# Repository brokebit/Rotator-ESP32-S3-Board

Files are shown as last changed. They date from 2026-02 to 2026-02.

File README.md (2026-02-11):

# Rotator-ESP32-S3-Board

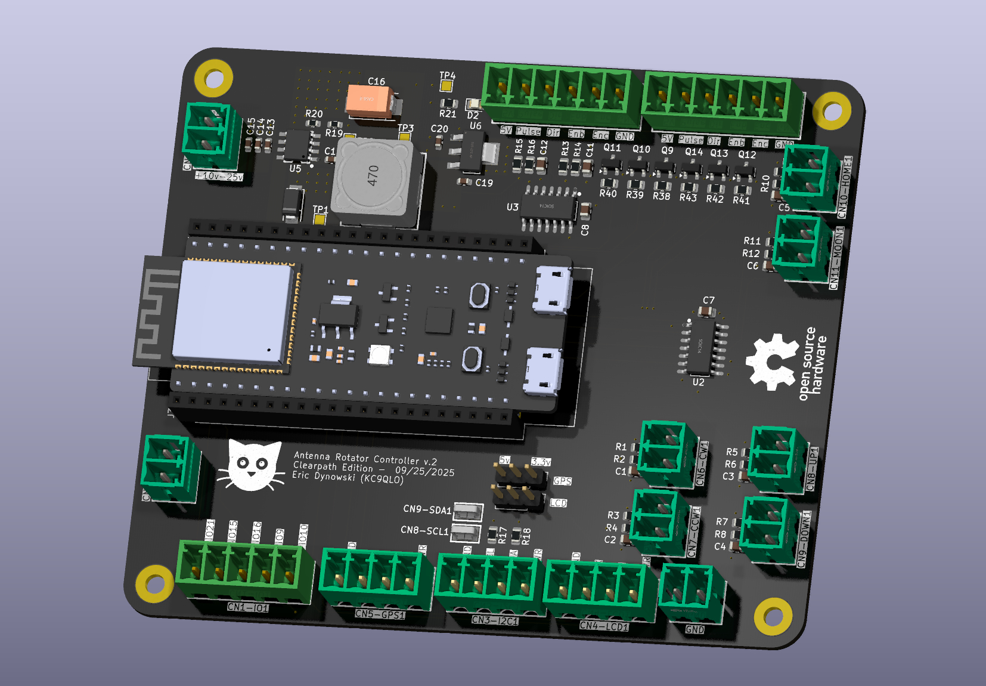
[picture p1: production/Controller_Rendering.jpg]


# Features / Design Info
- One of the ESP32 serial ports exposes a GS-232 interface for motor control commands for connecting to a PC interfacing with rotctld from the Hamlib suite
- GPS Time Sync using NEMA GPS Module over RS232
- Serial interface for Nextion Display
- Designed for Clearpath servo motors from https://teknic.com/
- Interface for 6 Hardware Debounced buttons for manual direction control, homing and moon tracking 
- Uses pulse encoder data from the Clearpath motors for position feedback
- Power input is +10v - +25v DC
- Motors are powered by seperate power source 
- Voltage select headers to select either 3.3v or 5v logic for RS232 interfaces (GPS, LCD)
- 6 Layer Board

# Build Pics
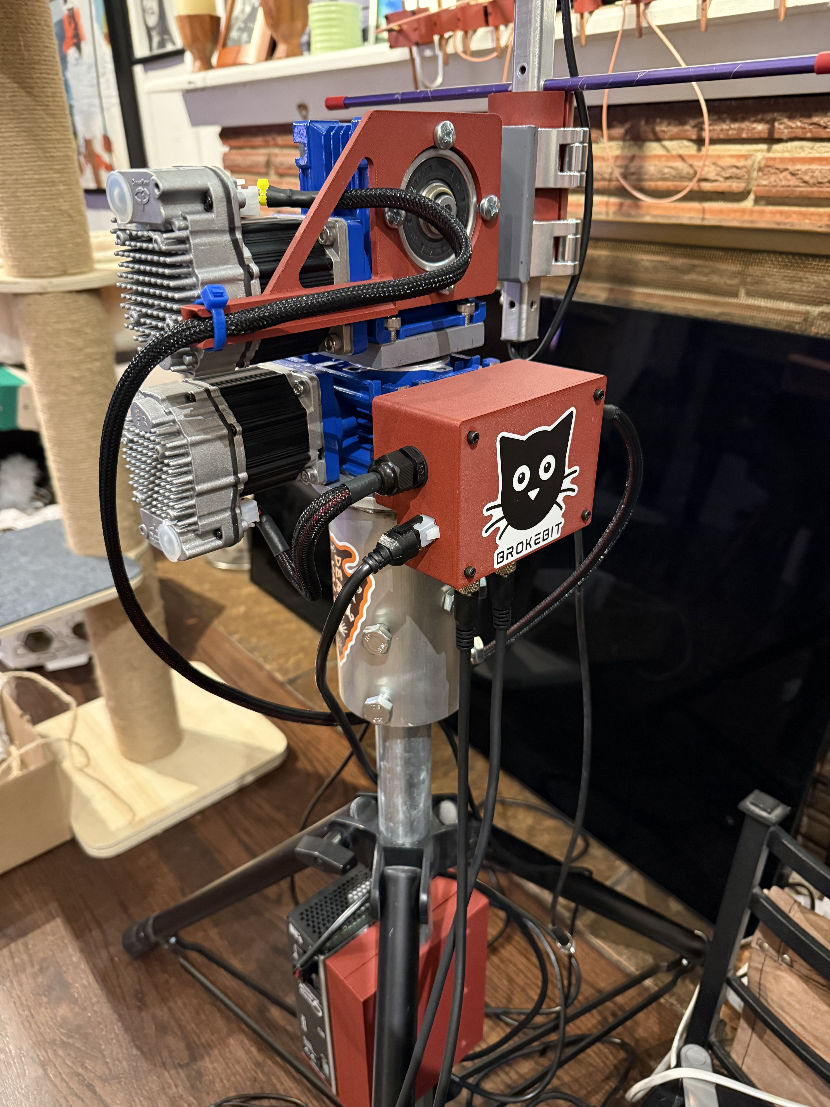
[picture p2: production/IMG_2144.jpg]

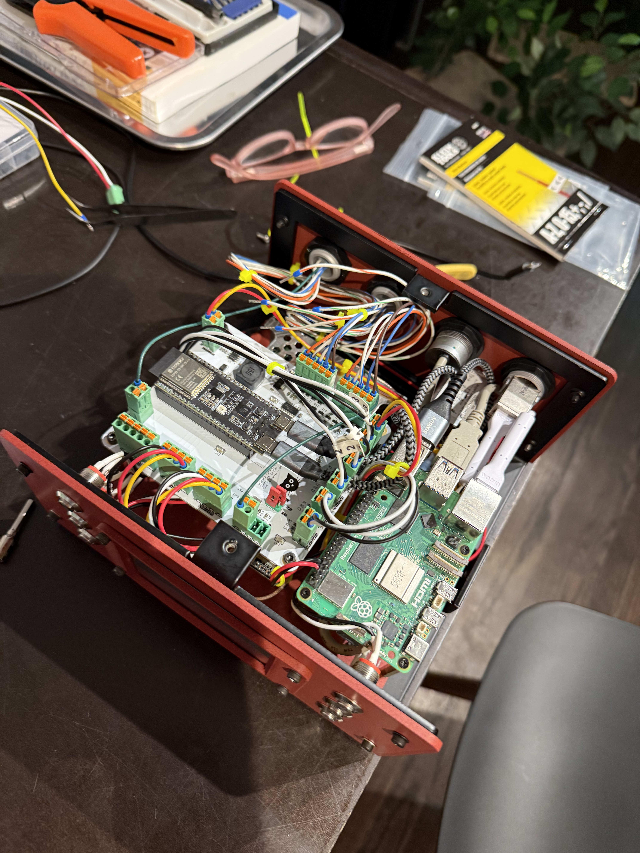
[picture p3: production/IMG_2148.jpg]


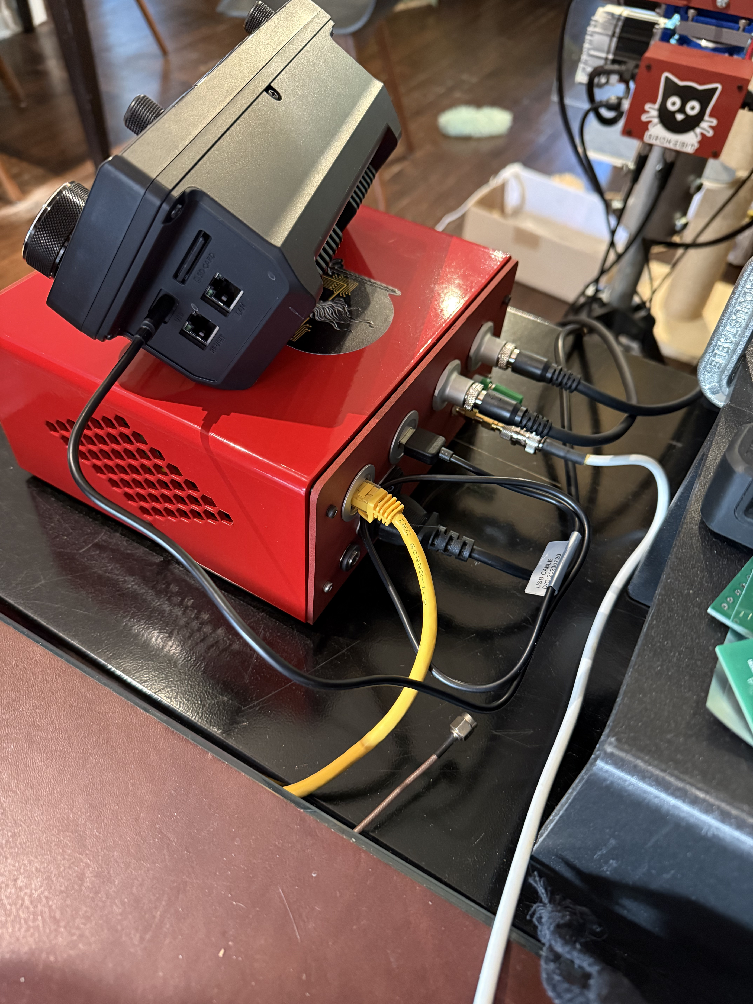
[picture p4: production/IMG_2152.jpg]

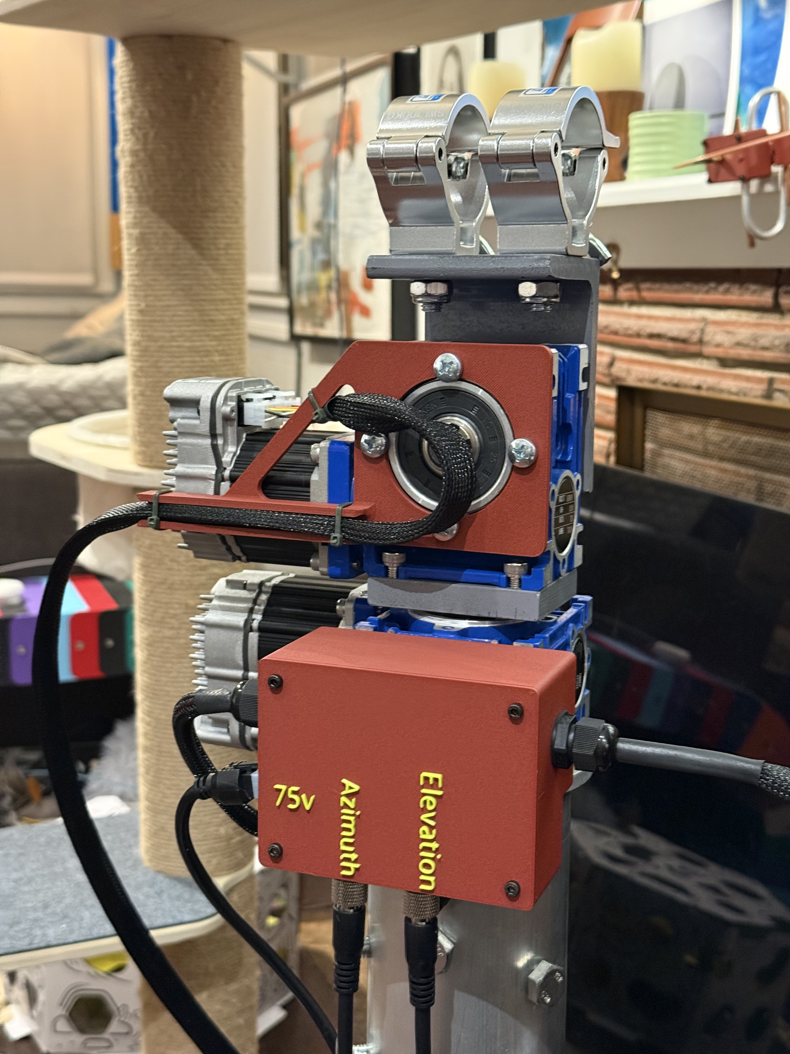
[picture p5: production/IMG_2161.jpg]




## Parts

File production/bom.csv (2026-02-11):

Designator | Footprint | Quantity | Value | LCSC Part #
C1, C11, C12, C2, C3, C4, C5, C6, C7, C8 | 0805 | 10 | .1uf
C13, C14, C15, C19, C20 | 0603 | 5 | 10uf
C16 | CAP-SMD_L7.3-W4.3-R-RD | 1 | 330uF | C79112
C17 | 0603 | 1 | 10nf
CN1-IO1 | CONN-TH_WJ15EDGVC-3.81-5P | 1 | WJ15EDGVC-3.81-5P | C8391
CN10-HOME1, CN11-MOON1, CN12-RST1, CN13-PWR2, CN5, CN6-CW1, CN7-CCW1, CN8-UP1, CN9-DOWN1 | CONN-TH_2P-P3.81_KF2EDGV-3.81-2P | 9 | KF2EDGV-3.81-2P | C441332
CN3-I2C1, CN4-LCD1, CN5-GPS1 | CONN-TH_4P-P3.81_WJ2EDGVC-3.81-4P | 3 | WJ15EDGVC-3.81-4P | C8410
CN8-SCL1, CN9-SDA1 | TESTPOINT-SMD_L3.8-W2.0_RH-5019 | 2 | RH-5019 | C5199800
D1 | SMA_L4.3-W2.6-LS5.1-RD | 1 | B340A | C64982
D2 | 0805 | 1 | LED | C84260
J1 | PinHeader_1x03_P2.54mm_Vertical | 1 | LCD_PWR_SELECT
J2 | PinHeader_1x03_P2.54mm_Vertical | 1 | GPS_PWR_SELECT
J3, J4 | PinSocket_1x22_P2.54mm_Vertical | 2 | Conn_01x22_Socket
L1 | IND-SMD_L12.5-W12.5_RLF12545T | 1 | 15uH | C40000
P1, P2 | CONN-TH_6P_WJ15EDGVC-3.81-6P | 2 | WJ15EDGVC-6P | C8415
Q10, Q11, Q12, Q13, Q14, Q9 | SOT-23 | 6 | MMBT3904
R1, R10, R11, R12, R13, R14, R15, R16, R17, R18, R2, R3, R4, R5, R6, R7, R8, R9 | 0805 | 18 | 10k
R19 | 0603 | 1 | 10k
R20 | 0603 | 1 | 3.24k
R21 | 0805 | 1 | 40 | C2930194
R38, R39, R40, R41, R42, R43 | 0805 | 6 | 4.7k
TP1, TP2, TP3, TP4 | TestPoint_Pad_1.5x1.5mm | 4 | TestPoint
U1 | ESP32-S3-DevKitC | 1 | ESP32-S3-DevKitC
U2, U3 | SOIC-14_L8.7-W3.9-P1.27-LS6.0-BL | 2 | 74HC14D,653 | C5605
U5 | ESOP-8_L4.9-W3.9-P1.27-LS6.0-TL-EP | 1 | TPS5430DDAR | C9864
U6 | SOT-223-4_L6.5-W3.5-P2.30-LS7.0-BR | 1 | AMS1117-3.3_C347222 | C347222

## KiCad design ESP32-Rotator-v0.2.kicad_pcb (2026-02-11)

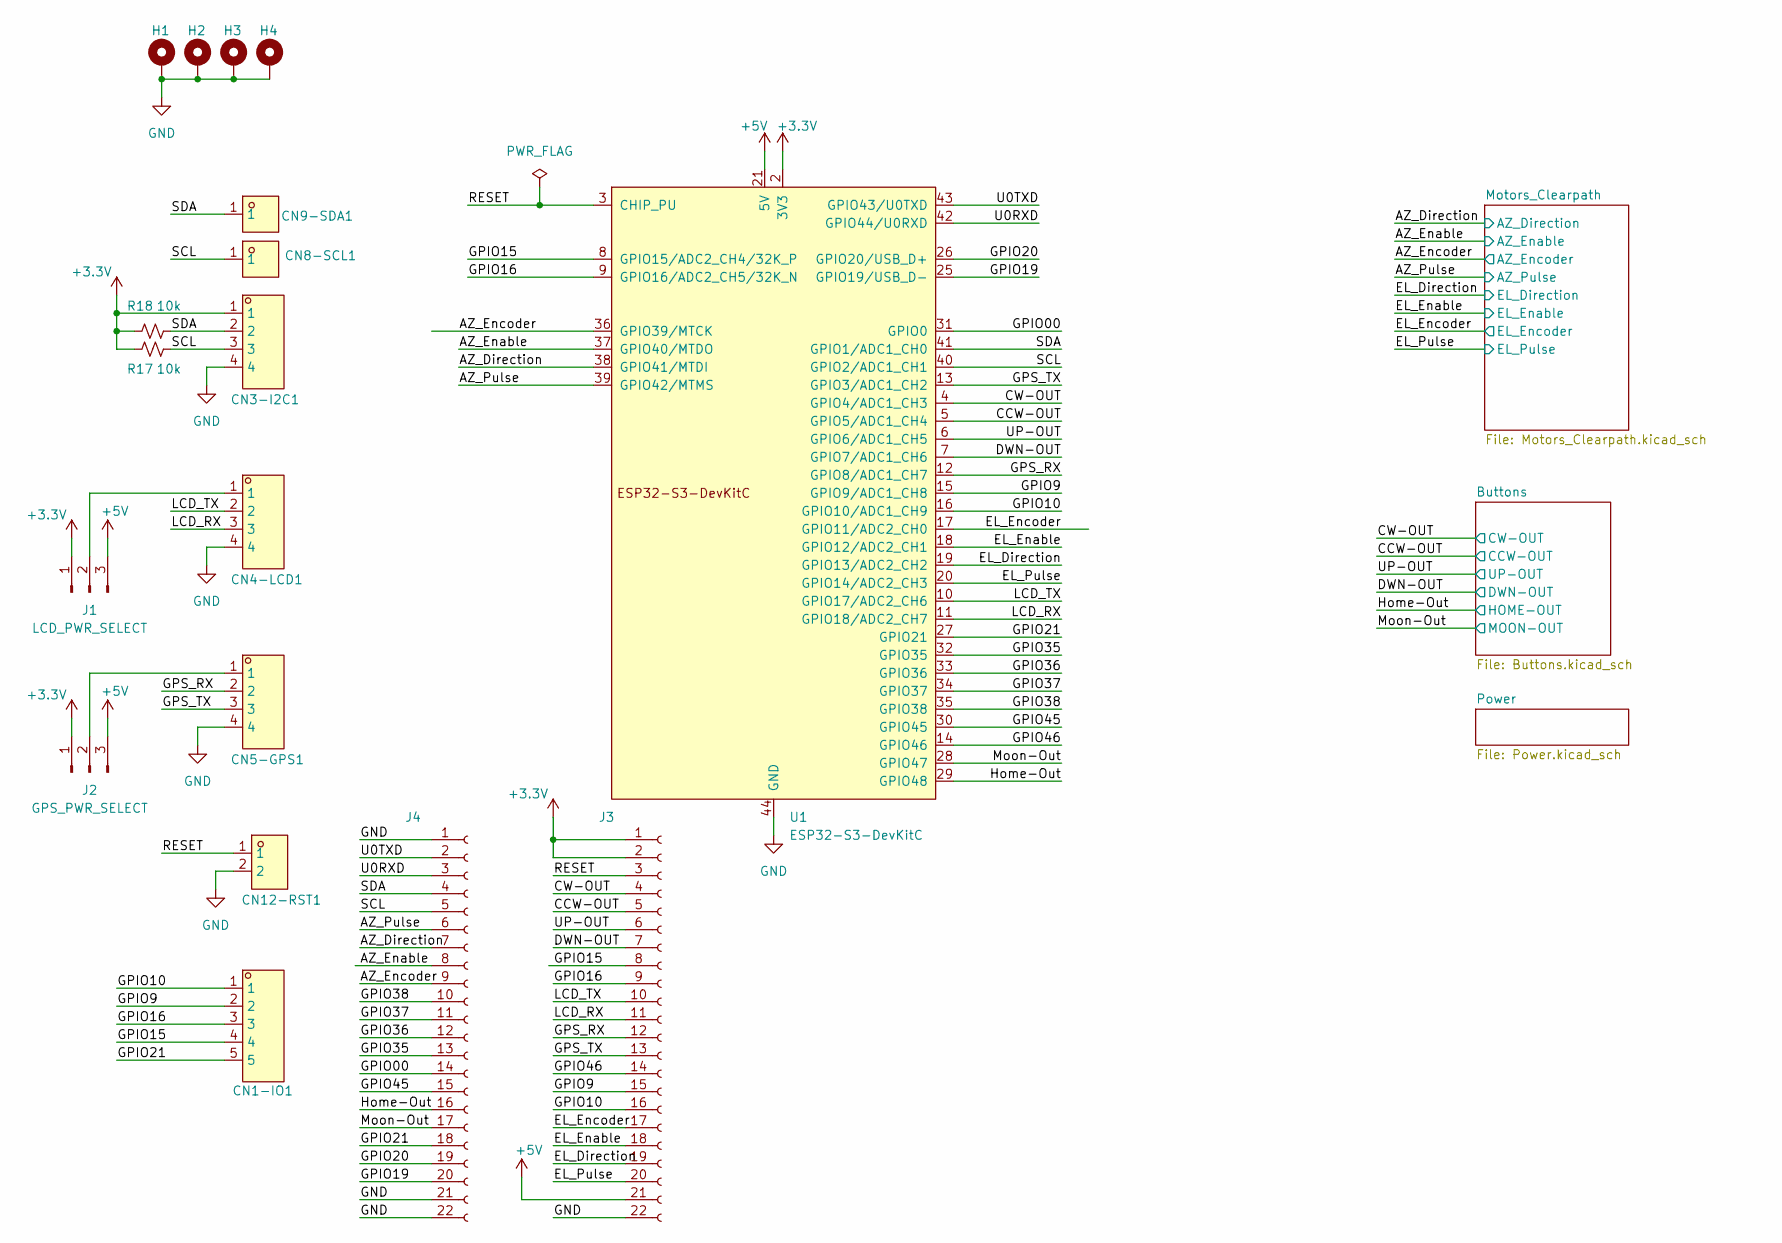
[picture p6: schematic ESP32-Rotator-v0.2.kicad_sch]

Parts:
CN1-IO1: WJ15EDGVC-3.81-5P; CONN-TH_WJ15EDGVC-3.81-5P; LCSC Part C8391
CN3-I2C1, CN4-LCD1, CN5-GPS1: WJ15EDGVC-3.81-4P; CONN-TH_4P-P3.81_WJ2EDGVC-3.81-4P; LCSC Part C8410
CN8-SCL1, CN9-SDA1: RH-5019; TESTPOINT-SMD_L3.8-W2.0_RH-5019; LCSC Part C5199800
CN12-RST1: KF2EDGV-3.81-2P; CONN-TH_2P-P3.81_KF2EDGV-3.81-2P; LCSC Part C441332
H1, H2, H3, H4: MountingHole_Pad; MountingHole_3.2mm_M3_Pad
J1: LCD_PWR_SELECT; PinHeader_1x03_P2.54mm_Vertical
J2: GPS_PWR_SELECT; PinHeader_1x03_P2.54mm_Vertical
J3, J4: Conn_01x22_Socket; PinSocket_1x22_P2.54mm_Vertical
R17, R18: 10k; R_0805_2012Metric
U1: ESP32-S3-DevKitC

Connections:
+3.3V: CN3-I2C1.1, J1.1, J2.1, J3.1, J3.2, R17.1, R18.1, U1.1 (3V3), U1.2 (3V3); also elsewhere on the board
+5V: J1.3, J2.3, J3.21, U1.21 (5V); also elsewhere on the board
/AZ_Direction: J4.7, U1.38 (GPIO41/MTDI); also elsewhere on the board
/AZ_Enable: J4.8, U1.37 (GPIO40/MTDO); also elsewhere on the board
/AZ_Encoder: J4.9, U1.36 (GPIO39/MTCK); also elsewhere on the board
/AZ_Pulse: J4.6, U1.39 (GPIO42/MTMS); also elsewhere on the board
/CCW-OUT: J3.5, U1.5 (GPIO5/ADC1_CH4); also elsewhere on the board
/CW-OUT: J3.4, U1.4 (GPIO4/ADC1_CH3); also elsewhere on the board
/DWN-OUT: J3.7, U1.7 (GPIO7/ADC1_CH6); also elsewhere on the board
/EL_Direction: J3.19, U1.19 (GPIO13/ADC2_CH2); also elsewhere on the board
/EL_Enable: J3.18, U1.18 (GPIO12/ADC2_CH1); also elsewhere on the board
/EL_Encoder: J3.17, U1.17 (GPIO11/ADC2_CH0); also elsewhere on the board
/EL_Pulse: J3.20, U1.20 (GPIO14/ADC2_CH3); also elsewhere on the board
/GPIO00: J4.14, U1.31 (GPIO0)
/GPIO9: CN1-IO1.2, J3.15, U1.15 (GPIO9/ADC1_CH8)
/GPIO10: CN1-IO1.1, J3.16, U1.16 (GPIO10/ADC1_CH9)
/GPIO15: CN1-IO1.4, J3.8, U1.8 (GPIO15/ADC2_CH4/32K_P)
/GPIO16: CN1-IO1.3, J3.9, U1.9 (GPIO16/ADC2_CH5/32K_N)
/GPIO19: J4.20, U1.25 (GPIO19/USB_D-)
/GPIO20: J4.19, U1.26 (GPIO20/USB_D+)
/GPIO21: CN1-IO1.5, J4.18, U1.27 (GPIO21)
/GPIO35: J4.13, U1.32 (GPIO35)
/GPIO36: J4.12, U1.33 (GPIO36)
/GPIO37: J4.11, U1.34 (GPIO37)
/GPIO38: J4.10, U1.35 (GPIO38)
/GPIO45: J4.15, U1.30 (GPIO45)
/GPIO46: J3.14, U1.14 (GPIO46)
/GPS_RX: CN5-GPS1.2, J3.12, U1.12 (GPIO8/ADC1_CH7)
/GPS_TX: CN5-GPS1.3, J3.13, U1.13 (GPIO3/ADC1_CH2)
/Home-Out: J4.16, U1.29 (GPIO48); also elsewhere on the board
/LCD_RX: CN4-LCD1.3, J3.11, U1.11 (GPIO18/ADC2_CH7)
/LCD_TX: CN4-LCD1.2, J3.10, U1.10 (GPIO17/ADC2_CH6)
/Moon-Out: J4.17, U1.28 (GPIO47); also elsewhere on the board
/RESET: CN12-RST1.1, J3.3, U1.3 (CHIP_PU)
/SCL: CN3-I2C1.3, CN8-SCL1.1, J4.5, R17.2, U1.40 (GPIO2/ADC1_CH1)
/SDA: CN3-I2C1.2, CN9-SDA1.1, J4.4, R18.2, U1.41 (GPIO1/ADC1_CH0)
/U0RXD: J4.3, U1.42 (GPIO44/U0RXD)
/U0TXD: J4.2, U1.43 (GPIO43/U0TXD)
/UP-OUT: J3.6, U1.6 (GPIO6/ADC1_CH5); also elsewhere on the board
GND: CN3-I2C1.4, CN4-LCD1.4, CN5-GPS1.4, CN12-RST1.2, H1.1, H2.1, H3.1, H4.1, J3.22, J4.1, J4.21, J4.22, U1.22 (GND), U1.23 (GND), U1.24 (GND), U1.44 (GND); also elsewhere on the board
unnamed: CN4-LCD1.1, J1.2
unnamed: CN5-GPS1.1, J2.2

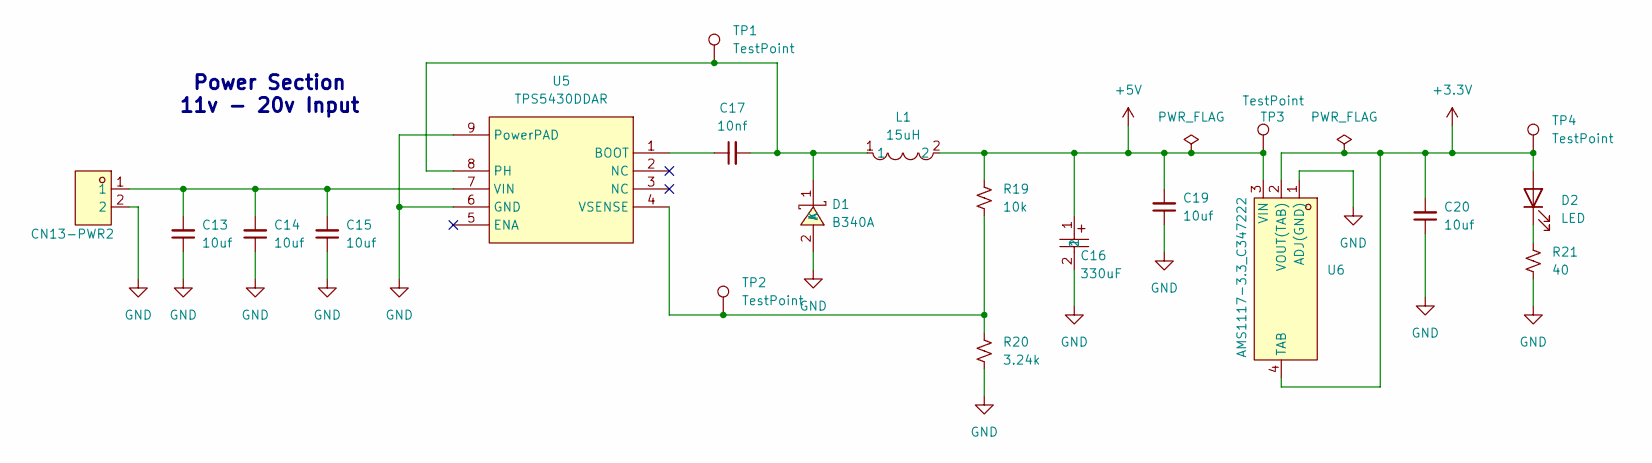
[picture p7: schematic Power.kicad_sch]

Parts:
C13, C14, C15, C19, C20: 10uf; C_0603_1608Metric
C16: 330uF; CAP-SMD_L7.3-W4.3-R-RD; LCSC Part C79112
C17: 10nf; C_0603_1608Metric
CN13-PWR2: KF2EDGV-3.81-2P; CONN-TH_2P-P3.81_KF2EDGV-3.81-2P; LCSC Part C441332
D1: B340A; SMA_L4.3-W2.6-LS5.1-RD; LCSC Part C64982
D2: LED; LED_0805_2012Metric; LCSC Part C84260
L1: 15uH; IND-SMD_L12.5-W12.5_RLF12545T; LCSC Part C40000
R19: 10k; R_0603_1608Metric
R20: 3.24k; R_0603_1608Metric
R21: 40; R_0805_2012Metric; LCSC Part C2930194
TP1, TP2, TP3, TP4: TestPoint; TestPoint_Pad_1.5x1.5mm
U5: TPS5430DDAR; ESOP-8_L4.9-W3.9-P1.27-LS6.0-TL-EP; LCSC Part C9864
U6: AMS1117-3.3_C347222; SOT-223-4_L6.5-W3.5-P2.30-LS7.0-BR; LCSC Part C347222

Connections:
+3.3V: C20.2, D2.2 (A), TP4.1, U6.2 (VOUT(TAB)), U6.4 (TAB); also elsewhere on the board
+5V: C16.1, C19.2, L1.2, R19.1, TP3.1, U6.3 (VIN); also elsewhere on the board
GND: C13.1, C14.1, C15.1, C16.2, C19.1, C20.1, CN13-PWR2.2, D1.2 (A), R20.2, R21.2, U5.6 (GND), U5.9 (PowerPAD), U6.1 (ADJ(GND)); also elsewhere on the board
unnamed: C17.2, D1.1 (K), L1.1, TP1.1, U5.8 (PH)
unnamed: D2.1 (K), R21.1
unnamed: C17.1, U5.1 (BOOT)
unnamed: C13.2, C14.2, C15.2, CN13-PWR2.1, U5.7 (VIN)
unnamed: R19.2, R20.1, TP2.1, U5.4 (VSENSE)

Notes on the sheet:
Power Section 11v - 20v Input

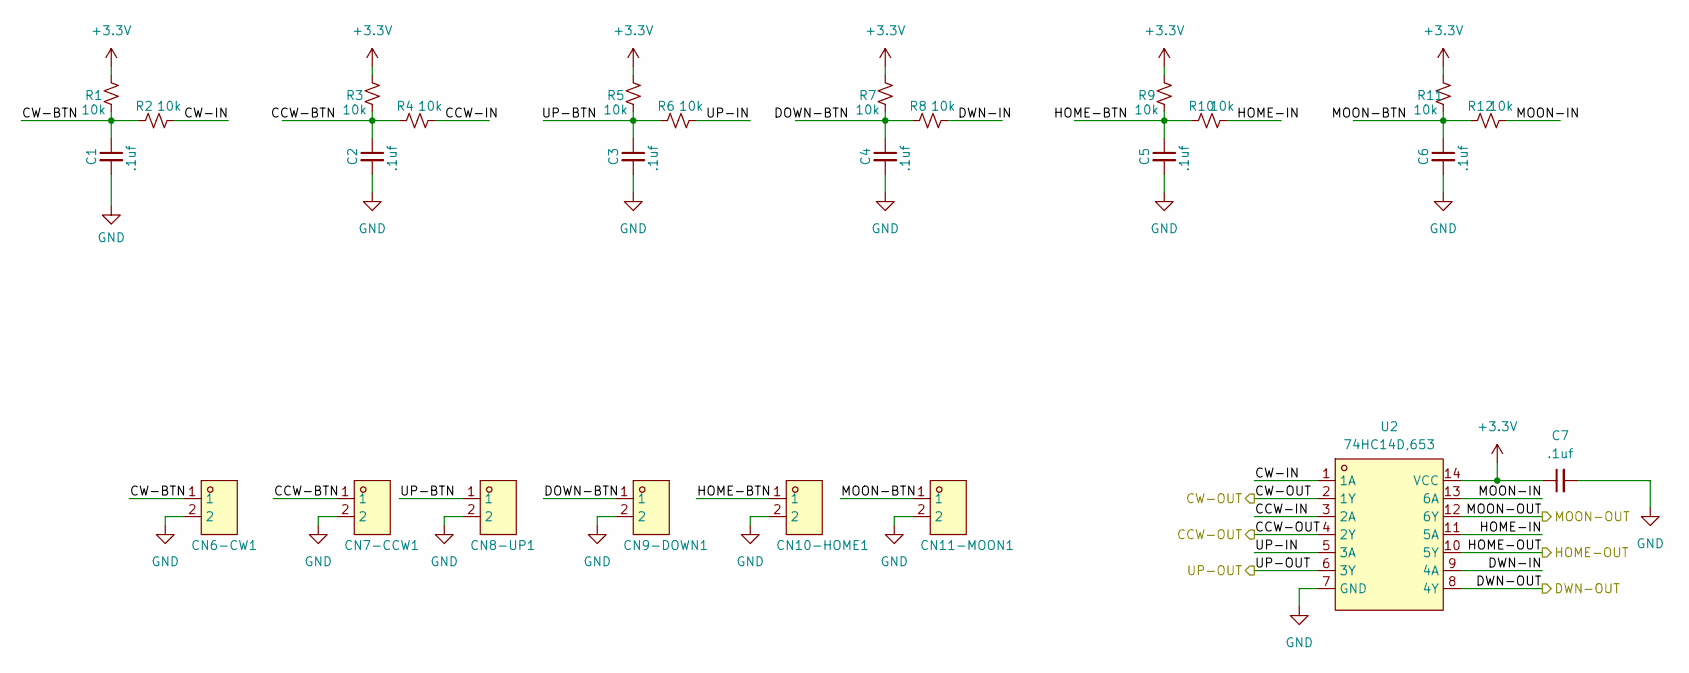
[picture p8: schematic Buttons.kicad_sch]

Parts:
C1, C2, C3, C4, C5, C6, C7: .1uf; C_0805_2012Metric
CN6-CW1, CN7-CCW1, CN8-UP1, CN9-DOWN1, CN10-HOME1, CN11-MOON1: KF2EDGV-3.81-2P; CONN-TH_2P-P3.81_KF2EDGV-3.81-2P; LCSC Part C441332
R1, R2, R3, R4, R5, R6, R7, R8, R9, R10, R11, R12: 10k; R_0805_2012Metric
U2: 74HC14D,653; SOIC-14_L8.7-W3.9-P1.27-LS6.0-BL; LCSC Part C5605

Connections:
+3.3V: C7.1, R1.1, R3.1, R5.1, R7.1, R9.1, R11.1, U2.14 (VCC); also elsewhere on the board
/Buttons/CCW-BTN: C2.1, CN7-CCW1.1, R3.2, R4.2
/Buttons/CCW-IN: R4.1, U2.3 (2A)
/Buttons/CW-BTN: C1.1, CN6-CW1.1, R1.2, R2.2
/Buttons/CW-IN: R2.1, U2.1 (1A)
/Buttons/DOWN-BTN: C4.1, CN9-DOWN1.1, R7.2, R8.2
/Buttons/DWN-IN: R8.1, U2.9 (4A)
/Buttons/HOME-BTN: C5.1, CN10-HOME1.1, R9.2, R10.2
/Buttons/HOME-IN: R10.1, U2.11 (5A)
/Buttons/MOON-BTN: C6.1, CN11-MOON1.1, R11.2, R12.2
/Buttons/MOON-IN: R12.1, U2.13 (6A)
/Buttons/UP-BTN: C3.1, CN8-UP1.1, R5.2, R6.2
/Buttons/UP-IN: R6.1, U2.5 (3A)
/CCW-OUT: U2.4 (2Y); also elsewhere on the board
/CW-OUT: U2.2 (1Y); also elsewhere on the board
/DWN-OUT: U2.8 (4Y); also elsewhere on the board
/Home-Out: U2.10 (5Y); also elsewhere on the board
/Moon-Out: U2.12 (6Y); also elsewhere on the board
/UP-OUT: U2.6 (3Y); also elsewhere on the board
GND: C1.2, C2.2, C3.2, C4.2, C5.2, C6.2, C7.2, CN6-CW1.2, CN7-CCW1.2, CN8-UP1.2, CN9-DOWN1.2, CN10-HOME1.2, CN11-MOON1.2, U2.7 (GND); also elsewhere on the board

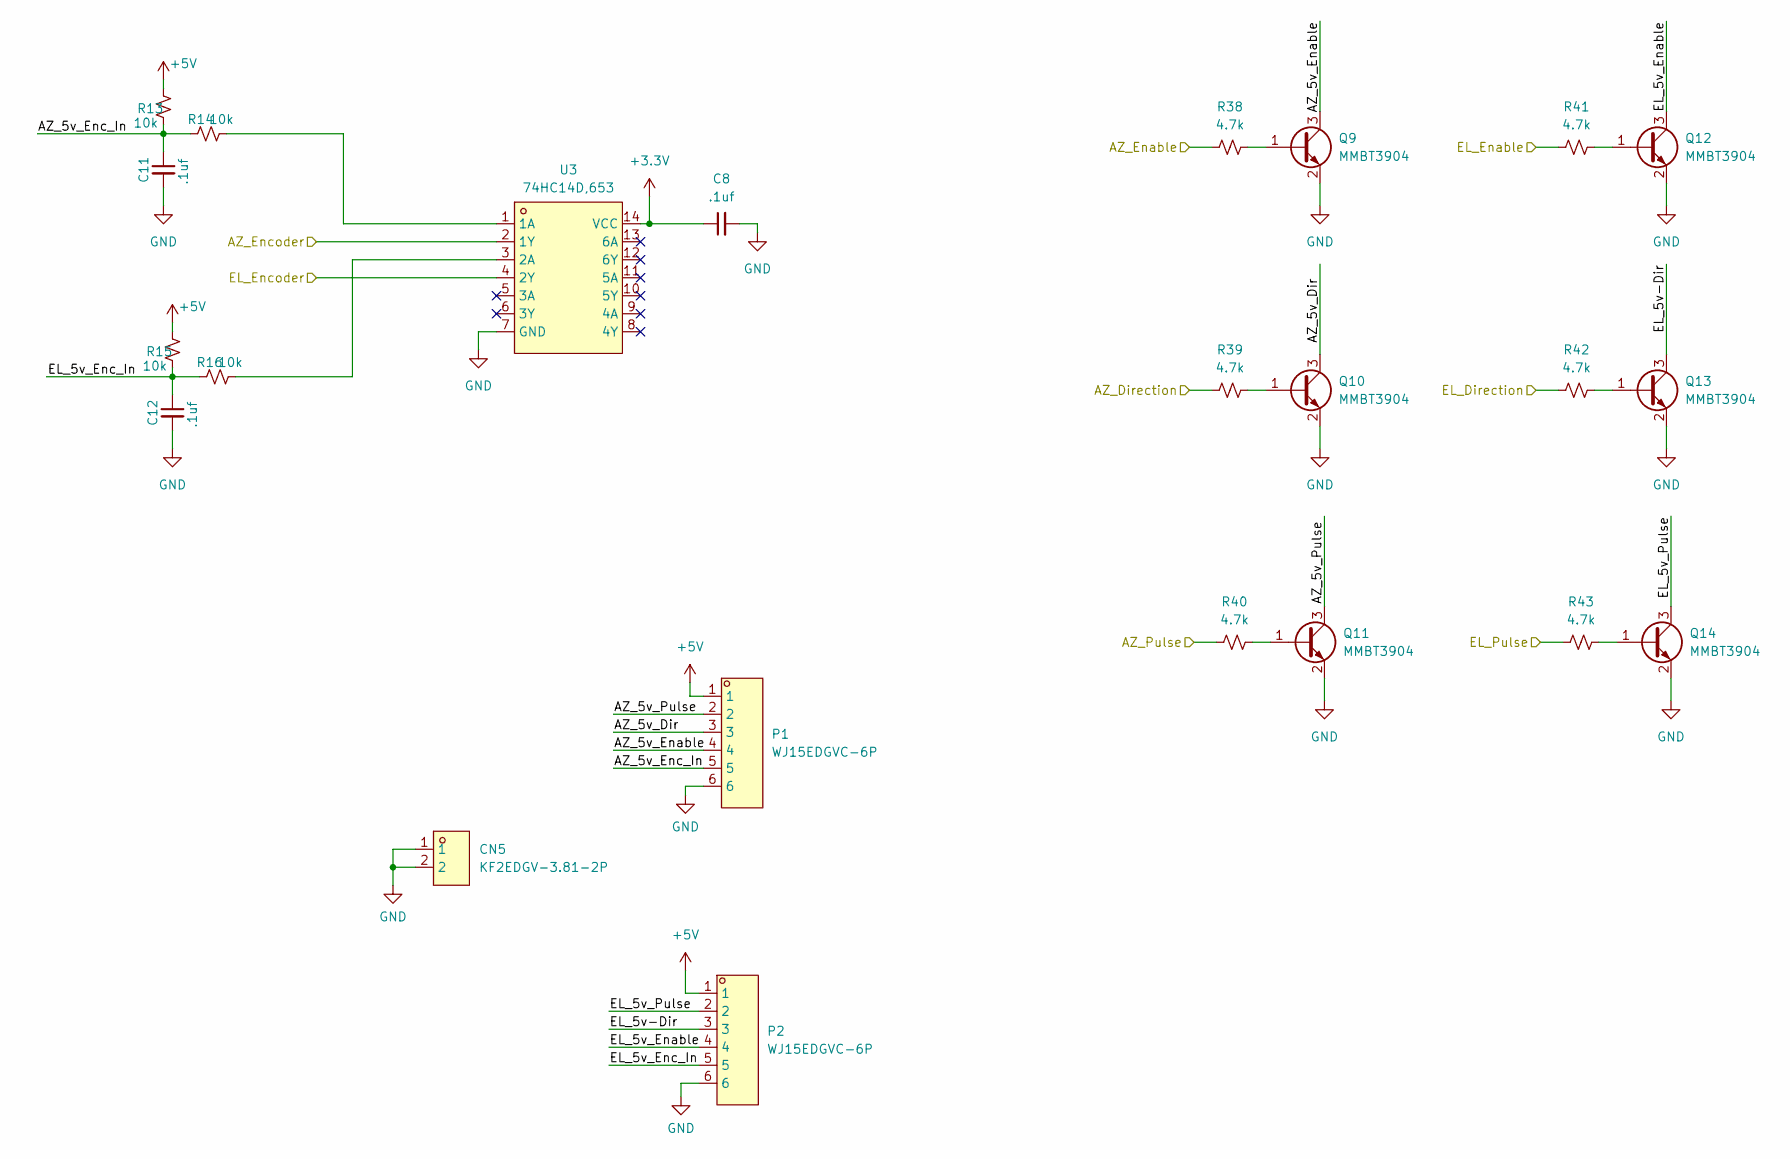
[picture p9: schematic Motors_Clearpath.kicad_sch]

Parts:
C8, C11, C12: .1uf; C_0805_2012Metric
CN5: KF2EDGV-3.81-2P; CONN-TH_2P-P3.81_KF2EDGV-3.81-2P; LCSC Part C441332
P1, P2: WJ15EDGVC-6P; CONN-TH_6P_WJ15EDGVC-3.81-6P; LCSC Part C8415
Q9, Q10, Q11, Q12, Q13, Q14: MMBT3904; SOT-23
R13, R14, R15, R16: 10k; R_0805_2012Metric
R38, R39, R40, R41, R42, R43: 4.7k; R_0805_2012Metric
U3: 74HC14D,653; SOIC-14_L8.7-W3.9-P1.27-LS6.0-BL; LCSC Part C5605

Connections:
+3.3V: C8.1, U3.14 (VCC); also elsewhere on the board
+5V: P1.1, P2.1, R13.1, R15.1; also elsewhere on the board
/AZ_Direction: R39.1; also elsewhere on the board
/AZ_Enable: R38.1; also elsewhere on the board
/AZ_Encoder: U3.2 (1Y); also elsewhere on the board
/AZ_Pulse: R40.1; also elsewhere on the board
/EL_Direction: R42.1; also elsewhere on the board
/EL_Enable: R41.1; also elsewhere on the board
/EL_Encoder: U3.4 (2Y); also elsewhere on the board
/EL_Pulse: R43.1; also elsewhere on the board
/Motors_Clearpath/AZ_5v_Dir: P1.3, Q10.3 (C)
/Motors_Clearpath/AZ_5v_Enable: P1.4, Q9.3 (C)
/Motors_Clearpath/AZ_5v_Enc_In: C11.1, P1.5, R13.2, R14.2
/Motors_Clearpath/AZ_5v_Pulse: P1.2, Q11.3 (C)
/Motors_Clearpath/EL_5v-Dir: P2.3, Q13.3 (C)
/Motors_Clearpath/EL_5v_Enable: P2.4, Q12.3 (C)
/Motors_Clearpath/EL_5v_Enc_In: C12.1, P2.5, R15.2, R16.2
/Motors_Clearpath/EL_5v_Pulse: P2.2, Q14.3 (C)
GND: C8.2, C11.2, C12.2, CN5.1, CN5.2, P1.6, P2.6, Q9.2 (E), Q10.2 (E), Q11.2 (E), Q12.2 (E), Q13.2 (E), Q14.2 (E), U3.7 (GND); also elsewhere on the board
unnamed: Q9.1 (B), R38.2
unnamed: Q10.1 (B), R39.2
unnamed: Q11.1 (B), R40.2
unnamed: Q12.1 (B), R41.2
unnamed: Q13.1 (B), R42.2
unnamed: Q14.1 (B), R43.2
unnamed: R14.1, U3.1 (1A)
unnamed: R16.1, U3.3 (2A)

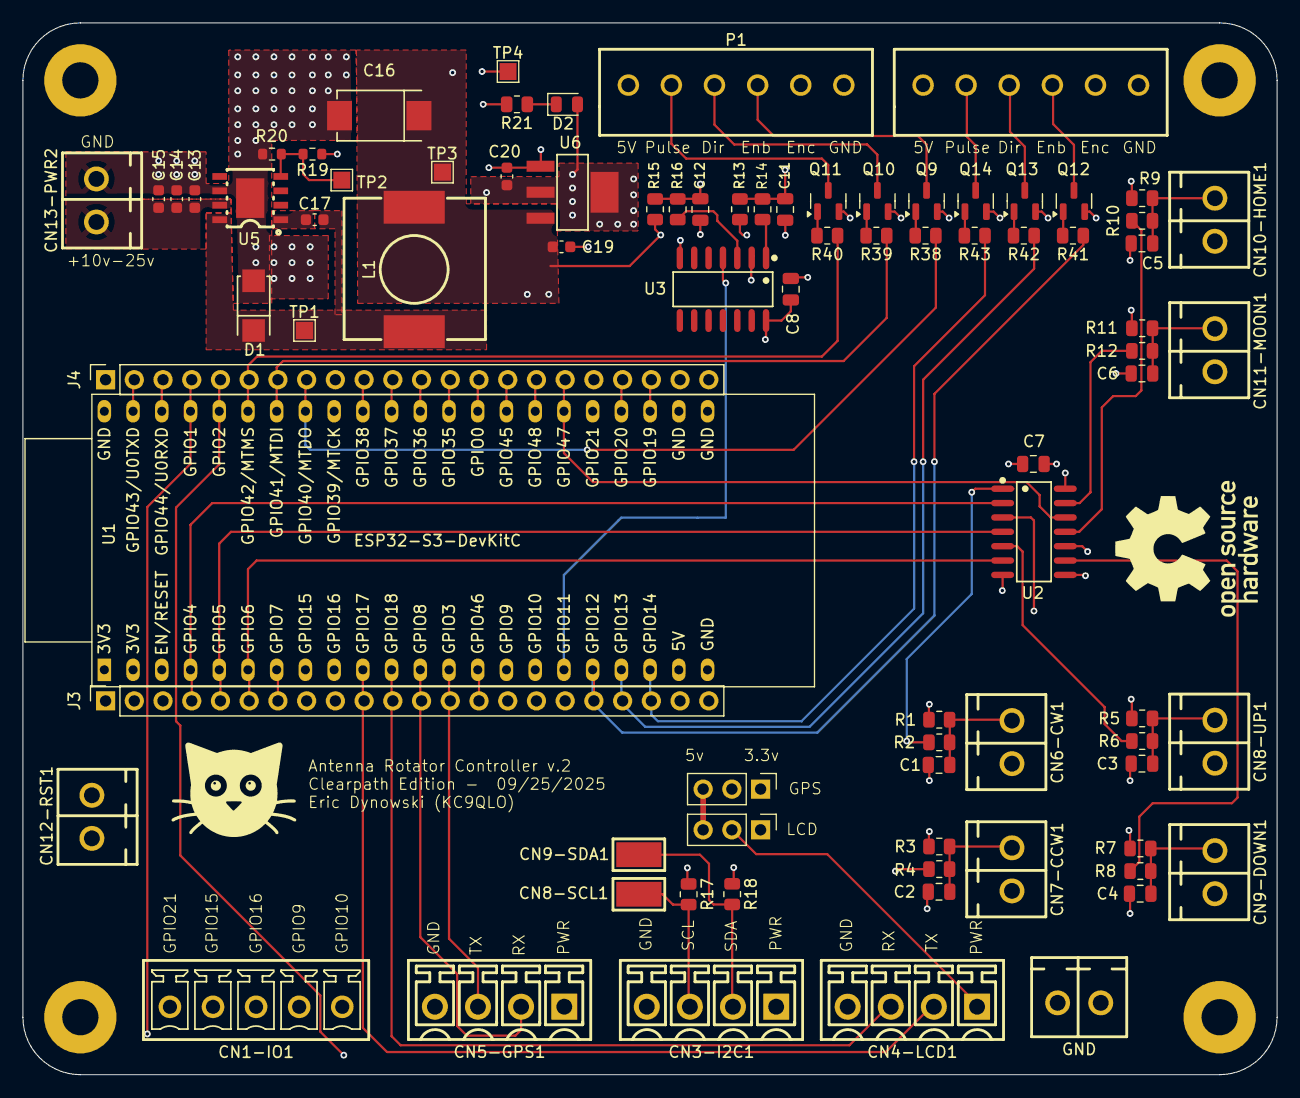
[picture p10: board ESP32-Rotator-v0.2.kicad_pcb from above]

Board: 6 copper layers, 110.9 x 93.0 mm, 87 parts (0 on the bottom side), 75 nets.
